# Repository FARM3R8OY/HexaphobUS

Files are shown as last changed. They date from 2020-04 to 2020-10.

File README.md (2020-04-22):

<div id="hexaphobus-logo" align="center">
    <br />
    HexaphobUS Logo
    <h1>HexaphobUS</h1>
    <h3>Hexapod robot | UdeS-GRO</h3>
</div>

[//]: # (------------------------------------------------)

<div id="badges" align="center">
    


 

</div>

[//]: # (------------------------------------------------)

**This is an academic project from robotic engineering undergraduates at Université de Sherbrooke. We are building a 6-axis robot from scratch with motion control, sequencing, and an intuitive user interface.**

<div id="robot" align="center">
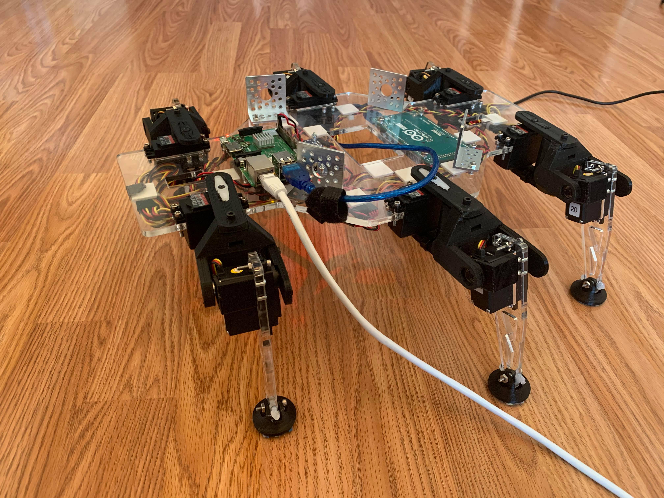
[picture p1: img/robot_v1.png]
Robot
    
</div>

## Table of Contents
- [Setup](#Setup)
    - [Setup for Users](#SetupUsers)
    - [Setup for Repository Contributors](#SetupContrib)
- [Documentation](#Documentation)
- [Robot Operation](#Operation)
- [External Resources](#Resources)
    - [Battery, Power Source, and Charger](#Battery)
    - [Crimping Tool Kit](#Crimp)
    - [Microcontroller Board](#Controller)
    - [On-Board Computer](#Computer)
    - [PWM Servo Driver](#PWM)
    - [Servomotor](#Servo)
    - [Voltage Regulator](#Regulator)
    
[//]: # (------------------------------------------------)

## Setup

#### Setup for Users

- Clone or download the repository;
- Connect the hexapod's microcontroller (Arduino) to your computer;
- Open the file ```hexaphobus_pwm.ino``` in the *./Code/hexaphobus_pwm* folder, and build the code into the microcontroller with your favorite IDE;
- Disconnect the microcontroller and connect the on-board computer (Raspberry Pi) instead (or connect remotely);
- Verify your Python version (3.5 and above);
- Run the file ```hexaphobus_ui.py``` in the *./Code/hexaphobus_ui* folder;
- Initialize the serial communication.

#### Setup for Repository Contributors

To setup the Git, the Key Management System and/or the Integrated Development Environment, head over to the [code setup file](./Code/setup.md). You can also add your own method, so the file can act as a setup archive for various softwares and operating systems.

To add new functions, refine the code, redesign the 3D model, and more, fork your own copy of the repository and [make a pull request after modifications](http://makeapullrequest.com).

## Documentation

All the code documentation can be found [here](https://raw.githack.com/gabrielcabana21/HexaphobUS/code/docs/html/index.html).

## Robot Operation

<div id="hexaphobus-ui" align="center">
    <br />
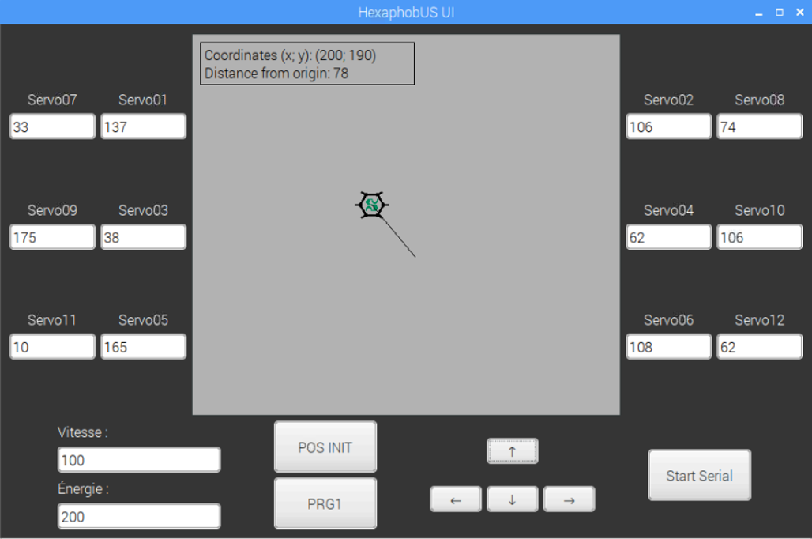
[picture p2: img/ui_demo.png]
HexaphobUS UI
    
</div>

- &#8593;: forward motion;
- &#8595;: backward motion;
- &#8592;: left turn;
- &#8594;: right turn;
- <kbd>POS INIT</kbd>: resets the robot origin;
- <kbd>PRG1</kbd>: pre-programmed motion sequence (currently unused);
- <kbd>Start Serial</kbd>: initializes serial communication with the robot;
- Servo ##: displays the servomotor angle (position of servos on the interface mimicks the robot seen from above);
- Vitesse / Énergie: robot speed and energy consumption (currently unused).

## External Resources

Under this section, you will find external links and descriptions of the project's external resources.

#### Battery, Power Source, and Charger
- Brand Name: Makita
- Model:
    - Battery: BL1041B
    - Power Source: PE00000028
    - Charger: DC10SB
- ASIN:
    - Battery: B017GQJDVM
    - Charger: B01FY4XCB0
- Information / Resources:
    - [Makita Battery Webpage](https://www.makitatools.com/products/details/BL1041B)
    - [Makita Power Source Webpage](https://www.makitatools.com/products/details/PE00000028)
    - [Makita Charger Webpage](https://www.makitatools.com/products/details/DC10SB)

#### Crimping Tool Kit
- Brand Name: Preciva Dupont
- Model: PR-3245 (SN-28B) + JST-XH
- ASIN: B07R1H3Z8X
- Information / Resources: [Amazon Link](https://www.amazon.com/gp/product/B07R1H3Z8X/)

#### Microcontroller Board
- Brand Name: Arduino
- Model: Mega 2560 R3 (A000067)
- ASIN: B0046AMGW0
- Information / Resources: [Arduino Webpage](https://store.arduino.cc/mega-2560-r3)

#### On-Board Computer
- Brand Name: Raspberry Pi
- Model: 3B
- ASIN: B01LPLPBS8
- Information / Resources: [Raspberry Pi Webpage](https://www.raspberrypi.org/products/raspberry-pi-3-model-b/)

#### PWM Servo Driver
- Brand Name: SunFounder
- Model: PCA9685
- ASIN: B014KTSMLA
- Information / Resources: [Sunfounder Wiki](http://wiki.sunfounder.cc/index.php?title=PCA9685_16_Channel_12_Bit_PWM_Servo_Driver)

#### Servomotor
- Brand Name: Hitec RCD
- Model: HS-422
- ASIN: B0006O3WWI
- Information / Resources: [Hitec Webpage](https://hitecrcd.com/products/servos/sport-servos/analog-sport-servos/hs-422/product)

#### Voltage Regulator
- Brand Name: DROK
- Model: 090483
- ASIN: B00C4QVTNU
- Information / Resources: [DROK Webpage](https://www.droking.com/Adjustable-High-Power-Adapter-Buck-Voltage-Regulator-DC8-40V-to-1.25-36V-8A-100W-Converter-Laptop-Charger)

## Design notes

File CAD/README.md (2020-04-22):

## Parts and Assemblies
- Assemblies:
  - [V1](./V1)
  - [V2](./V2)
  - [V3](./V3)
- Internal resources (homemade components):
  - [V1](./V1/Internal)
  - [V2](./V2/Internal)
  - [V3](./V3/Internal)
- [External resources](./External)
- [Files for laser cutting](./Cutting)

The hexapod was designed with only a coxa motor and a tibia motor, omitting the femur motor to minimise the power requirement. Most motion types should be feasible, albeit a little more limited. Legs on each side of the body are designed symmetrically to align the feet and facilitate the body design (mirrored sketches). They each contain a foot, two motors, two bearings and their mounts, a joint and its two attachments, and some screws and bolts. The hexapod assembly contains six legs, three of which are mirrored, an on-board computer, a microcontroller board, a voltage regulator, a PWM servo driver, a battery, and some fasteners.

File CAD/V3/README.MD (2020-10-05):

<div id="hexaphobus-robot-v3-hex" align="center">
    <br />
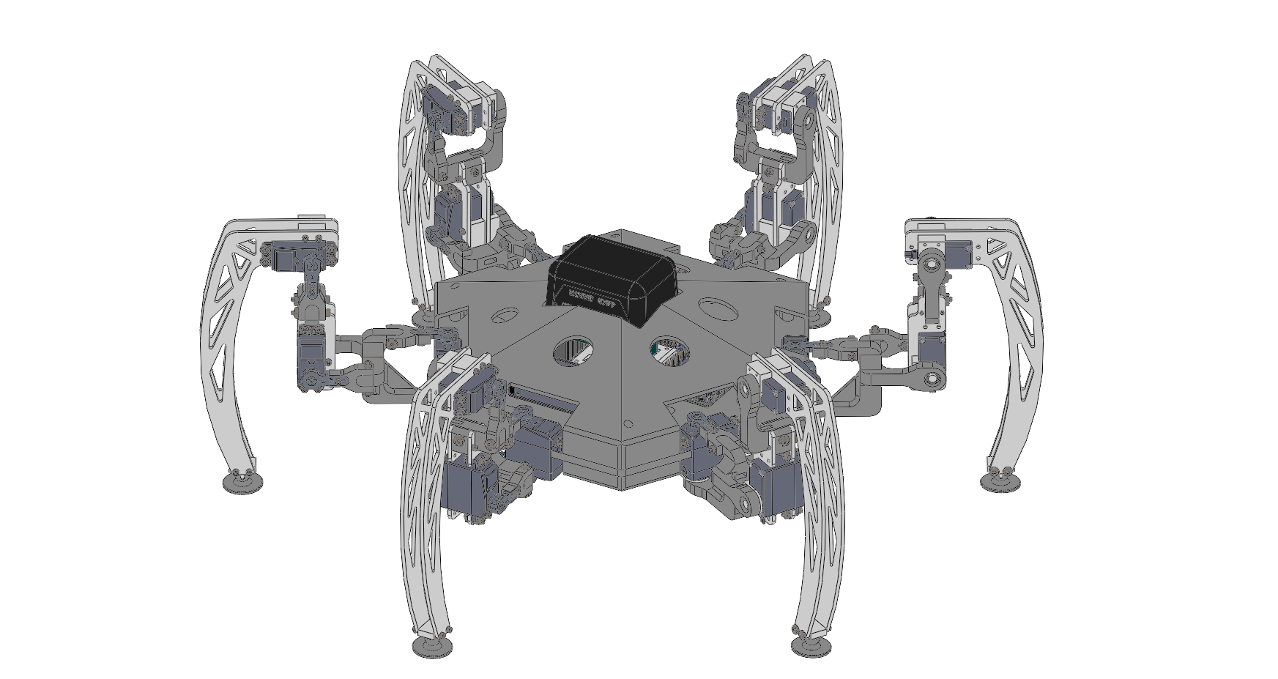
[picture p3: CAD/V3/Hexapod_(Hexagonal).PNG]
HexaphobUS Robot (V3, Hexagonal)
    
</div>

<div id="hexaphobus-robot-v3-18m" align="center">
    <br />
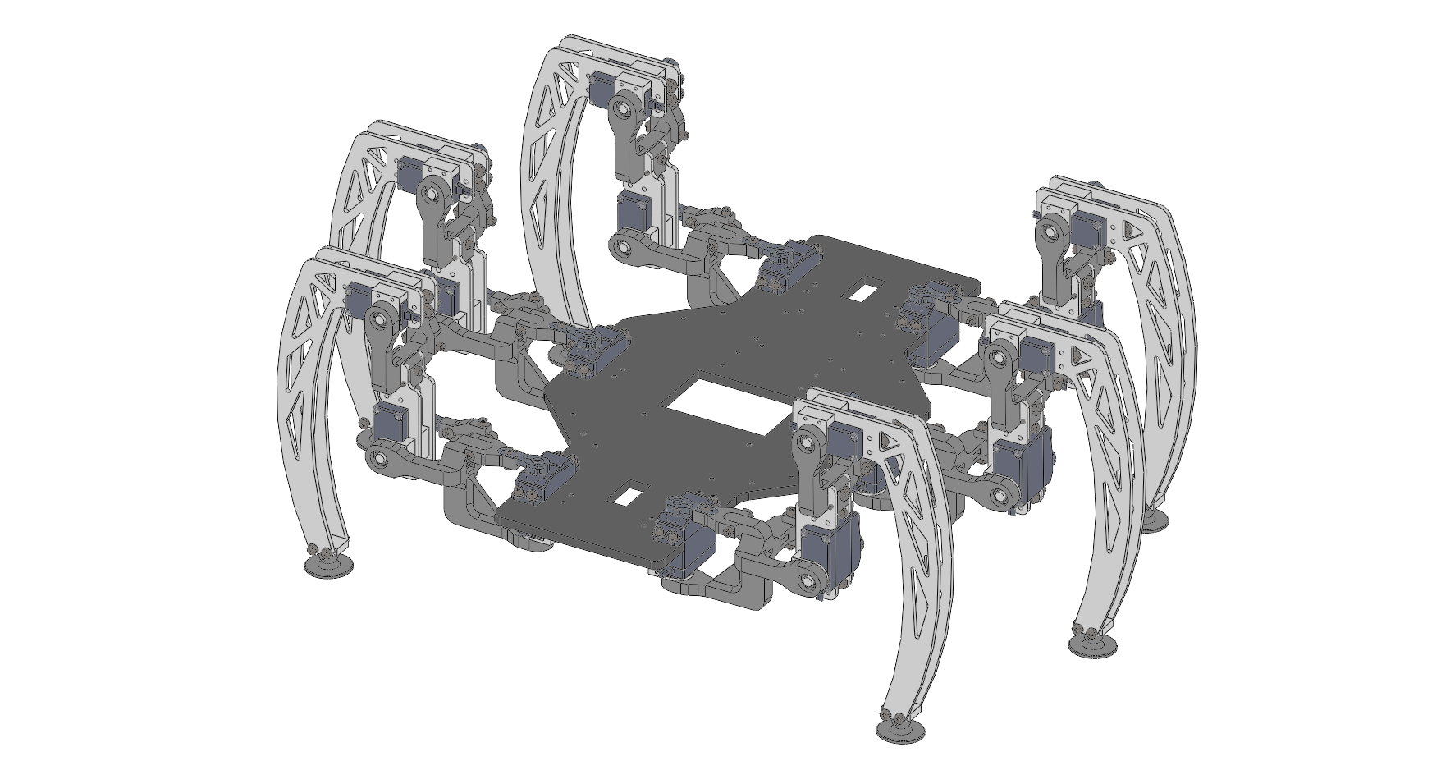
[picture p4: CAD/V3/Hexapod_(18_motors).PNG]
HexaphobUS Robot (V3, 18 Motors)
    
</div>

<div id="hexaphobus-robot-v3-12m" align="center">
    <br />
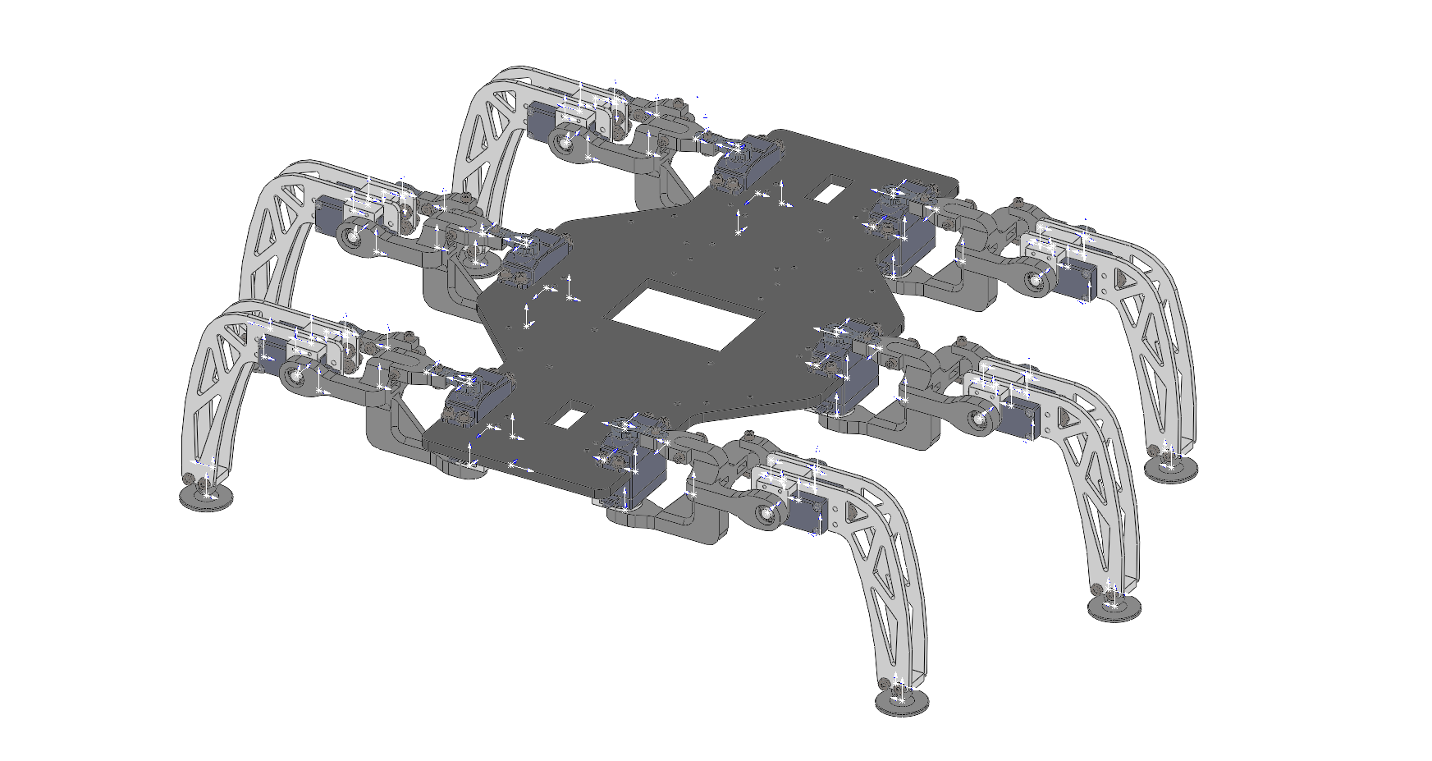
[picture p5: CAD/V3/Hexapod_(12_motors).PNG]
HexaphobUS Robot (V3, 12 Motors)
    
</div>

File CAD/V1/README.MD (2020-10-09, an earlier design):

<div id="hexaphobus-robot-v1-curved" align="center">
    <br />
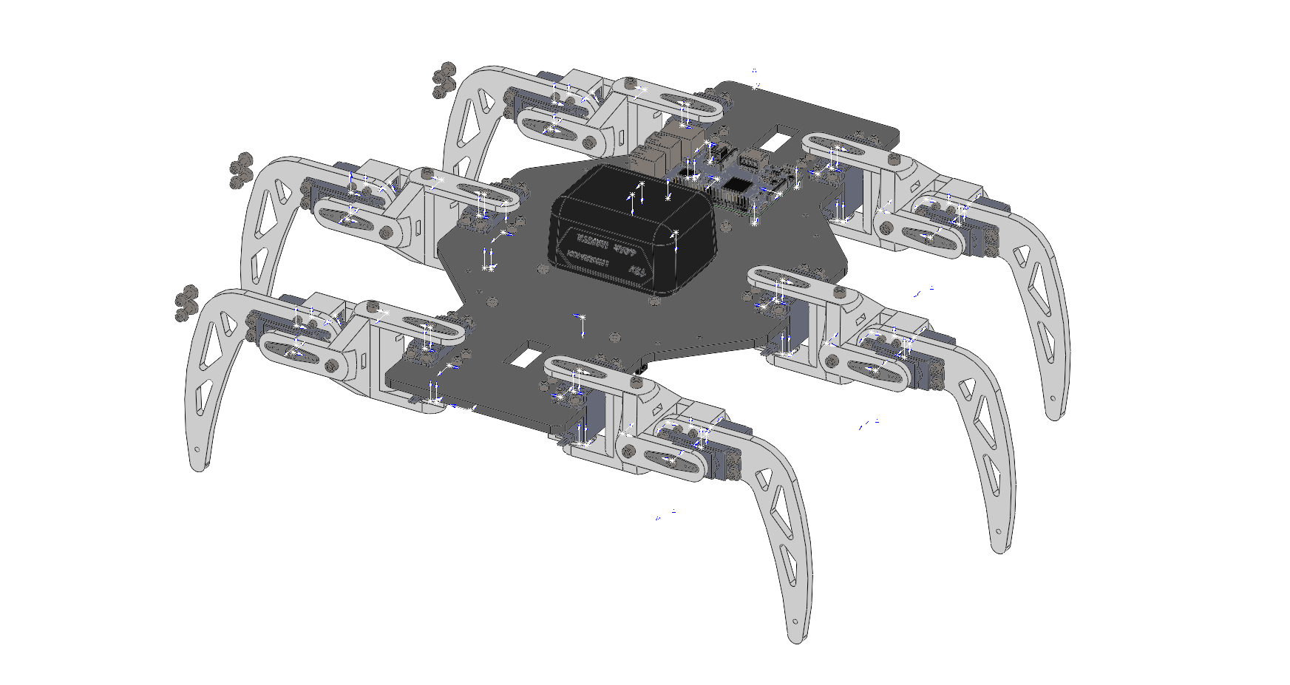
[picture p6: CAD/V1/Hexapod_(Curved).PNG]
HexaphobUS Robot (V1, Curved Legs)
    
</div>

<div id="hexaphobus-robot-v1-straight" align="center">
    <br />
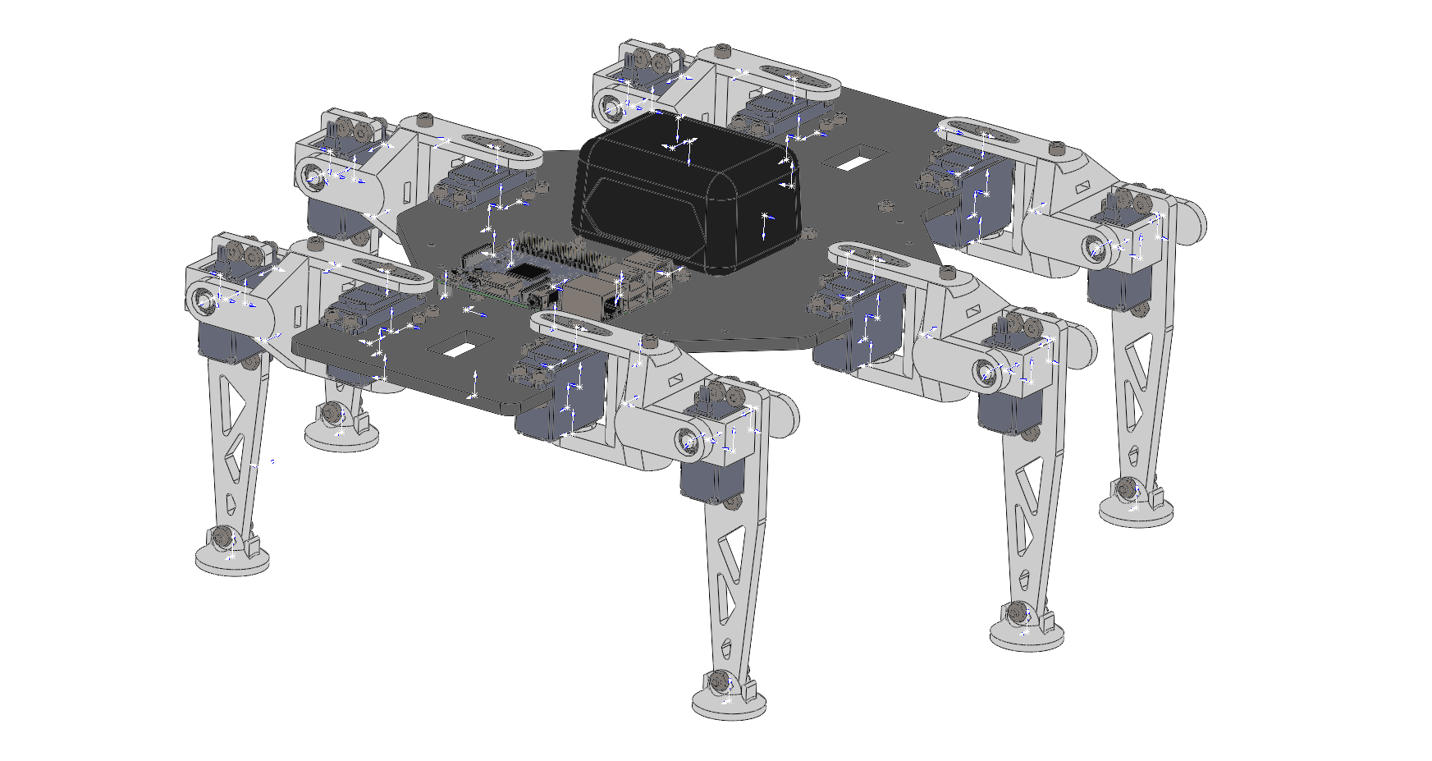
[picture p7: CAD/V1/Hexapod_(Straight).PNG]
HexaphobUS Robot (V1, Straight Legs)
    
</div>

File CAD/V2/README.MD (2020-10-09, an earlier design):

<div id="hexaphobus-robot-v2" align="center">
    <br />
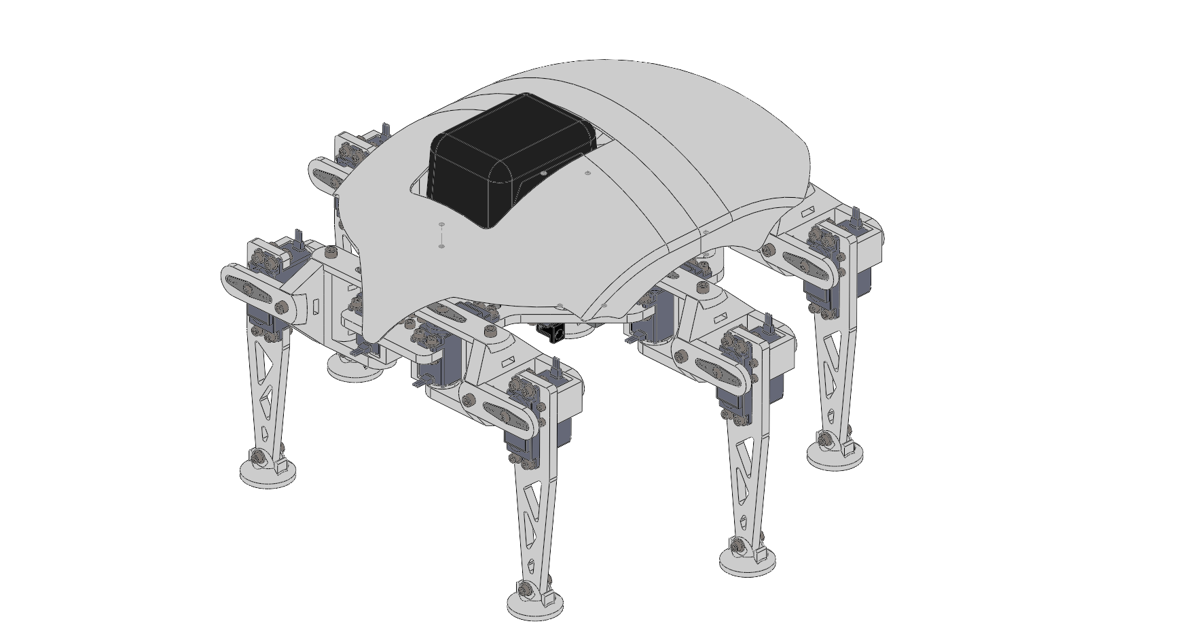
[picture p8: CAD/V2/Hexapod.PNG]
HexaphobUS Robot (V2)
    
</div>

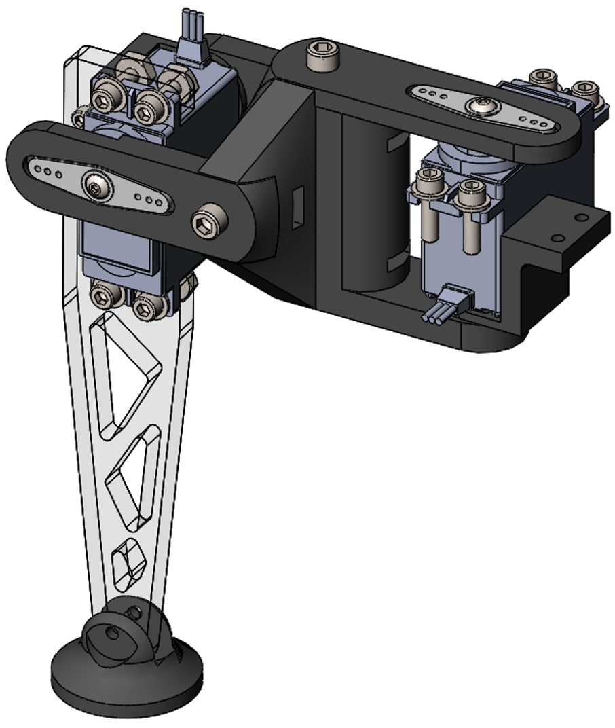
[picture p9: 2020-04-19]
img/leg_design_v2.png

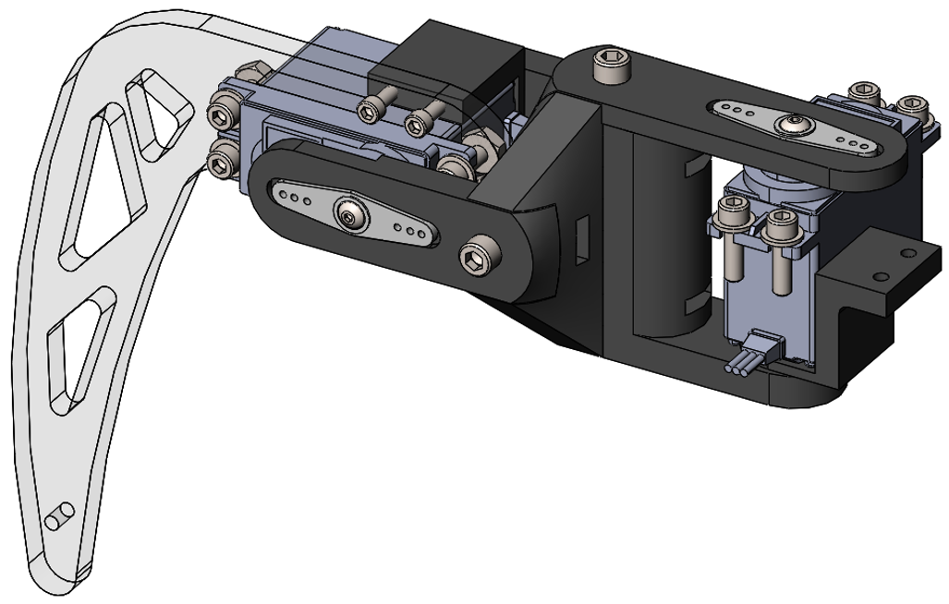
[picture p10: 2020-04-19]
img/leg_design_v1_(1).png

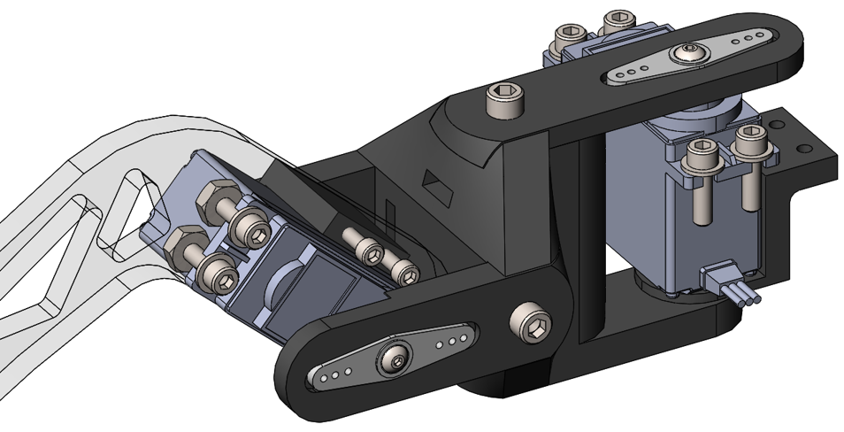
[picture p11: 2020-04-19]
img/leg_design_v1_(2).png

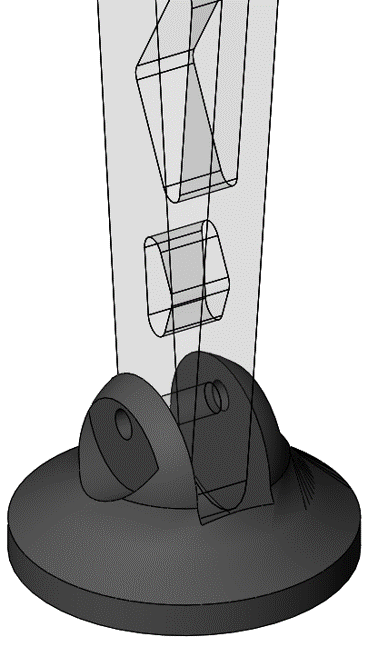
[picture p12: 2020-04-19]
img/slippers.png

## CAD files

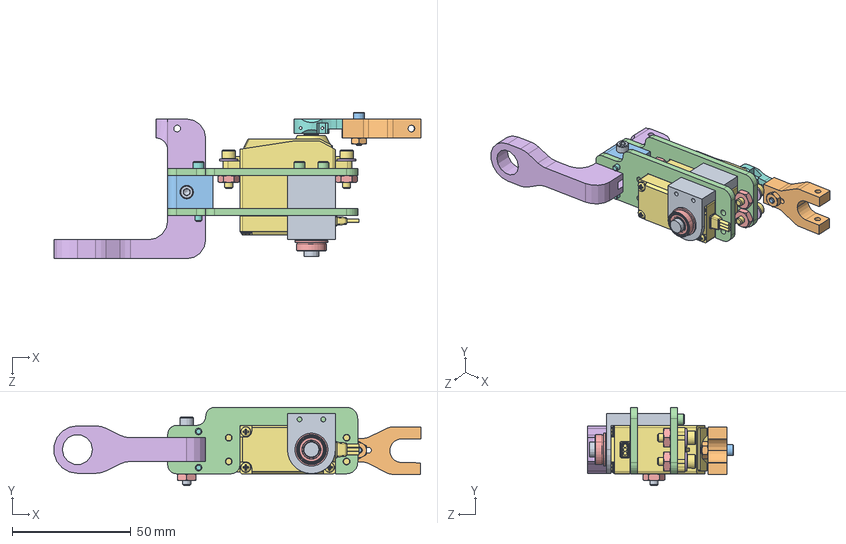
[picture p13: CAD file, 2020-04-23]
CAD/V3/Tibia_(Mirror).SLDASM
154.5 x 33.0 x 61.6 mm
Link
Horn_attachment
Joint_attachment_(Tibia)
Tibia x 2
Bearing
Joint_(Tibia_to_foot)
DS3225MG
Horn
Bearing_mount_(Foot)
MSHXNUT 0.112-40-D-N
HX-SHCS 0.112-40x0.4375x0.4375-N
HX-SHCS 0.112-40x1x0.75-N x 2
MSHXNUT 0.138-32-D-N x 5
Narrow FW 0.138 x 4
HX-SHCS 0.138-32x0.5x0.5-N x 4
HX-SHCS 0.112-40x0.875x0.875-N x 2
HX-SHCS 0.138-32x1x1-N

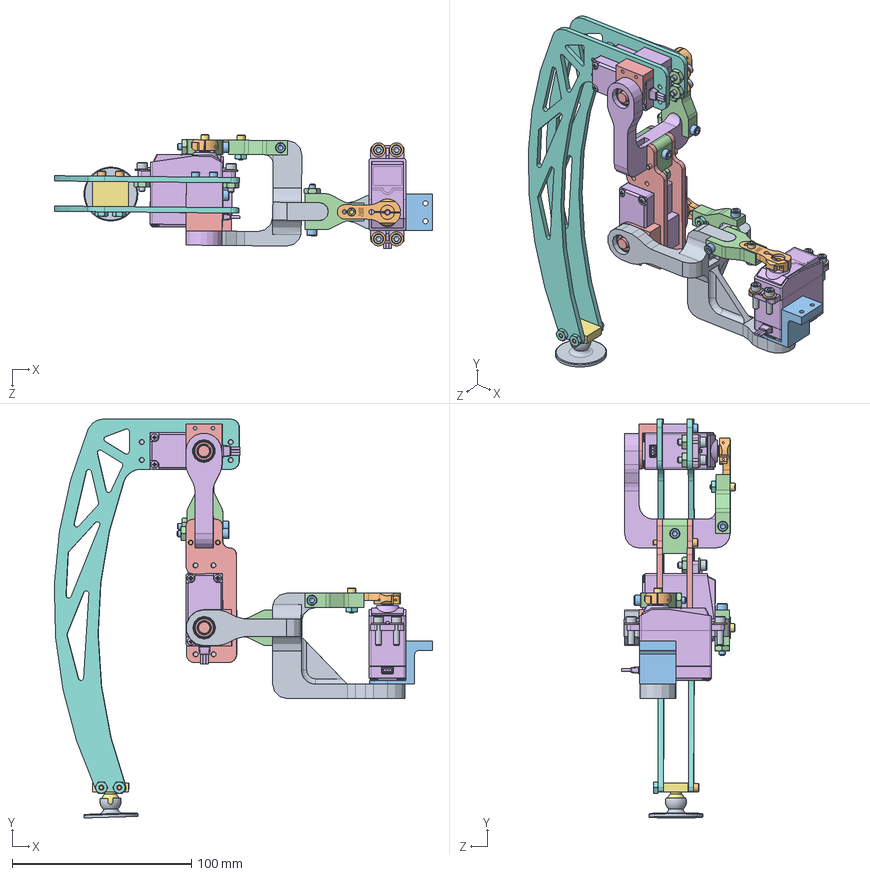
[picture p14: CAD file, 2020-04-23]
CAD/V3/Foot+Tibia+Femur_(Mirror).SLDASM
210.9 x 222.5 x 63.4 mm
Joint_(Femur_to_tibia)_(Mirror)
Horn x 3
Bearing_mount_(Femur)
Horn_attachment x 3
Bearing x 3
DS3225MG x 3
HX-SHCS 0.112-40x0.4375x0.4375-N x 3
MSHXNUT 0.112-40-D-N x 5
HX-SHCS 0.138-32x0.5x0.5-N x 12
Narrow FW 0.138 x 12
HX-SHCS 0.138-32x1x1-N x 4
MSHXNUT 0.138-32-D-N x 12
Bearing_mount_(Foot) x 2
Link x 2
Joint_(Foot_to_slipper)
Foot_(Long) x 2
Slipper
HX-SHCS 0.112-40x0.875x0.875-N x 4
HX-SHCS 0.112-40x1x0.75-N x 4
Joint_attachment_(Tibia)
Tibia x 2
Joint_(Tibia_to_foot)

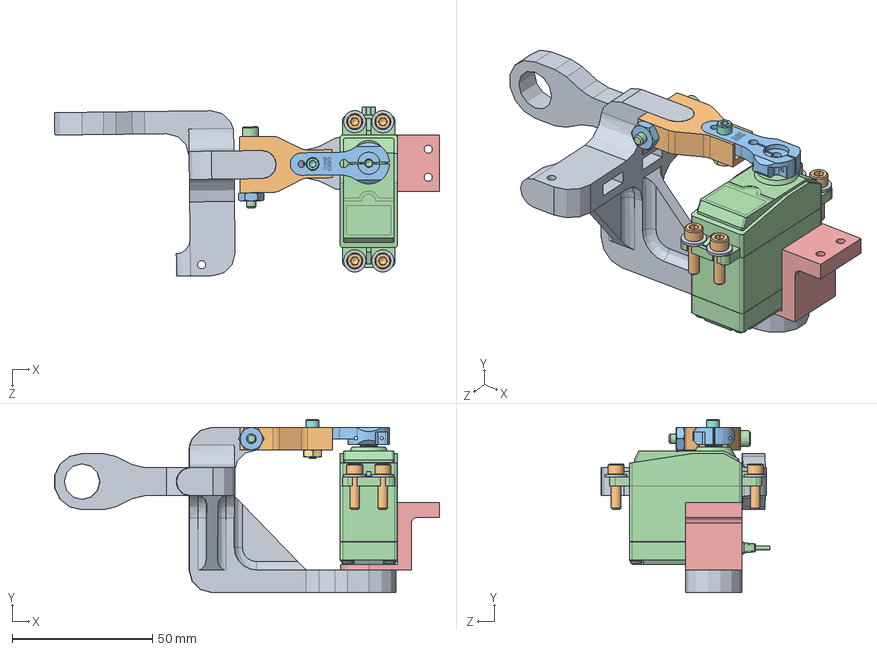
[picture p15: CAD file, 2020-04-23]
CAD/V3/Femur.SLDASM
137.2 x 61.6 x 60.3 mm
Joint_(Femur_to_tibia)
Horn_attachment
Horn
DS3225MG
Bearing_mount_(Femur)
Bearing
MSHXNUT 0.112-40-D-N
HX-SHCS 0.112-40x0.4375x0.4375-N
Narrow FW 0.138 x 4
HX-SHCS 0.138-32x0.5x0.5-N x 4
MSHXNUT 0.138-32-D-N
HX-SHCS 0.138-32x1x1-N

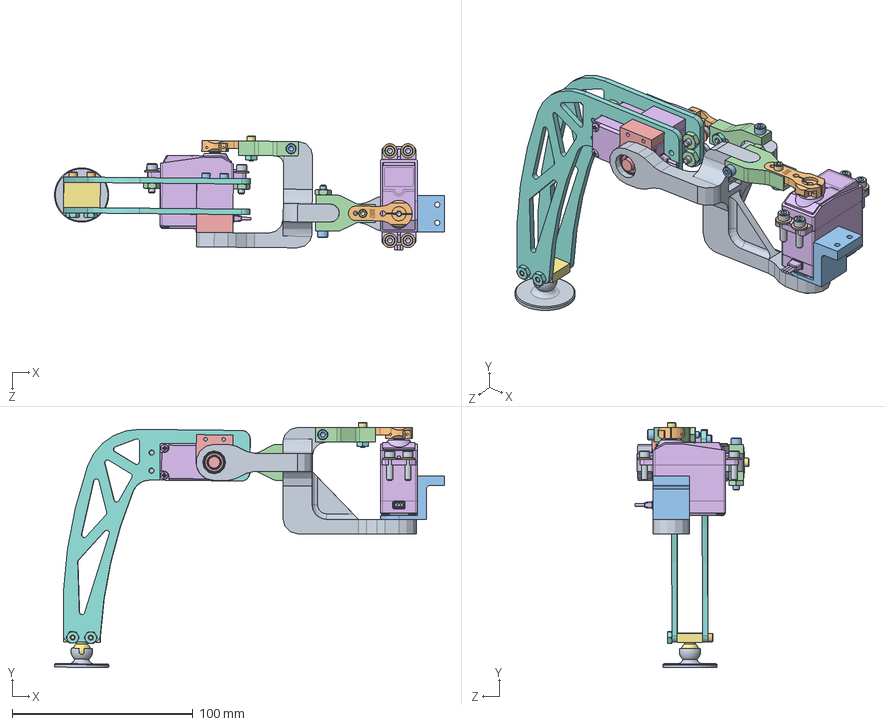
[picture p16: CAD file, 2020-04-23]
CAD/V3/Foot+Femur_(Mirror).SLDASM
215.7 x 135.7 x 63.2 mm
Joint_(Femur_to_tibia)_(Mirror)
Horn x 2
Bearing_mount_(Femur)
Horn_attachment x 2
Bearing x 2
DS3225MG x 2
HX-SHCS 0.112-40x0.4375x0.4375-N x 2
MSHXNUT 0.112-40-D-N x 4
HX-SHCS 0.138-32x0.5x0.5-N x 8
Narrow FW 0.138 x 8
HX-SHCS 0.138-32x1x1-N x 2
MSHXNUT 0.138-32-D-N x 6
Bearing_mount_(Foot)
Link
Joint_(Foot_to_slipper)
Foot_(Short) x 2
Slipper
HX-SHCS 0.112-40x0.875x0.875-N x 2
HX-SHCS 0.112-40x1x0.75-N x 2

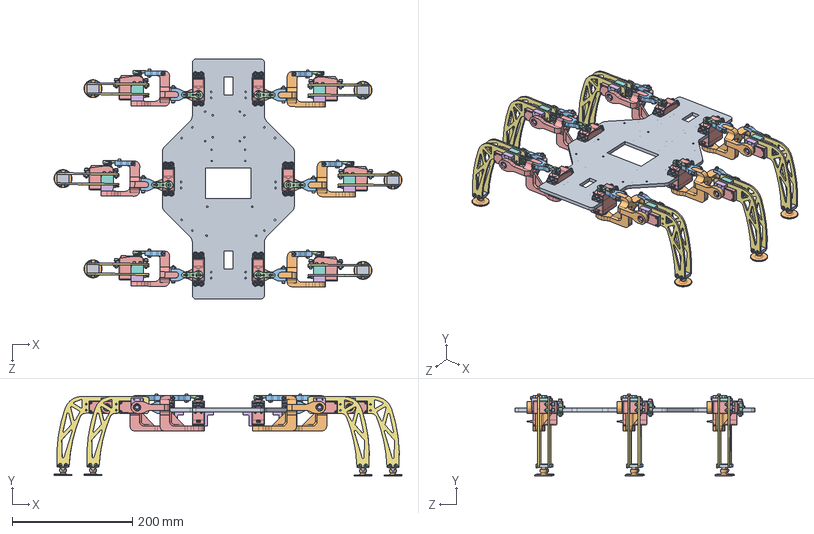
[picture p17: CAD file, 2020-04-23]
CAD/V3/Hexapod_(12_motors).SLDASM
579.5 x 136.5 x 400.0 mm
Joint_(Femur_to_tibia) x 3
Horn_attachment x 12
Horn x 12
DS3225MG x 12
Bearing_mount_(Femur) x 6
Bearing x 12
MSHXNUT 0.112-40-D-N x 24
HX-SHCS 0.112-40x0.4375x0.4375-N x 12
Narrow FW 0.138 x 48
HX-SHCS 0.138-32x0.5x0.5-N x 48
MSHXNUT 0.138-32-D-N x 36
HX-SHCS 0.138-32x1x1-N x 12
Bearing_mount_(Foot) x 6
Foot_(Short) x 12
Link x 6
Joint_(Foot_to_slipper) x 6
Slipper x 6
HX-SHCS 0.112-40x0.875x0.875-N x 12
HX-SHCS 0.112-40x1x0.75-N x 12
Joint_(Femur_to_tibia)_(Mirror) x 3

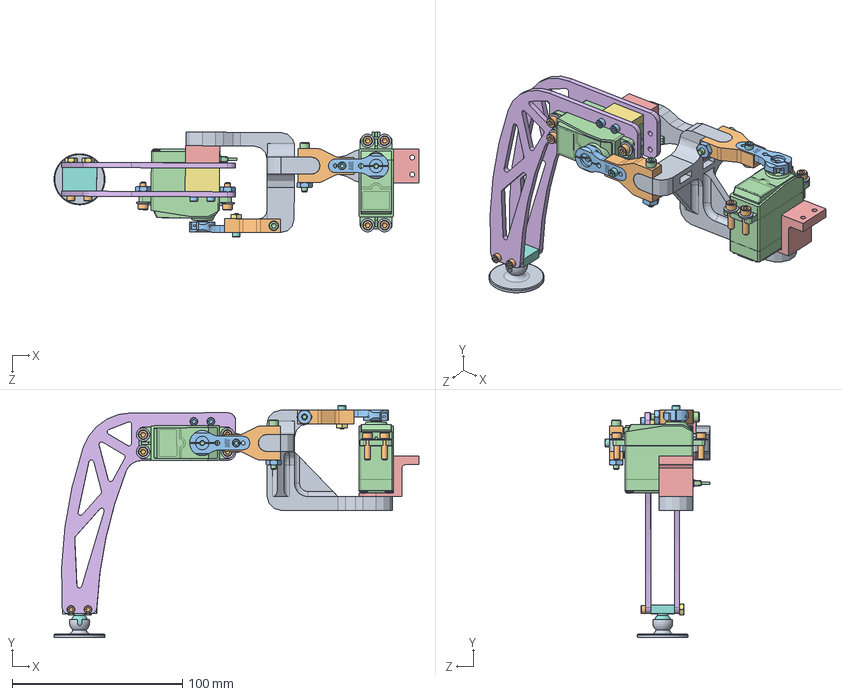
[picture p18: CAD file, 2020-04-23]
CAD/V3/Foot+Femur.SLDASM
214.5 x 136.5 x 62.0 mm
Joint_(Femur_to_tibia)
Horn_attachment x 2
Horn x 2
DS3225MG x 2
Bearing_mount_(Femur)
Bearing x 2
MSHXNUT 0.112-40-D-N x 4
HX-SHCS 0.112-40x0.4375x0.4375-N x 2
Narrow FW 0.138 x 8
HX-SHCS 0.138-32x0.5x0.5-N x 8
MSHXNUT 0.138-32-D-N x 6
HX-SHCS 0.138-32x1x1-N x 2
Bearing_mount_(Foot)
Foot_(Short) x 2
Link
Joint_(Foot_to_slipper)
Slipper
HX-SHCS 0.112-40x0.875x0.875-N x 2
HX-SHCS 0.112-40x1x0.75-N x 2

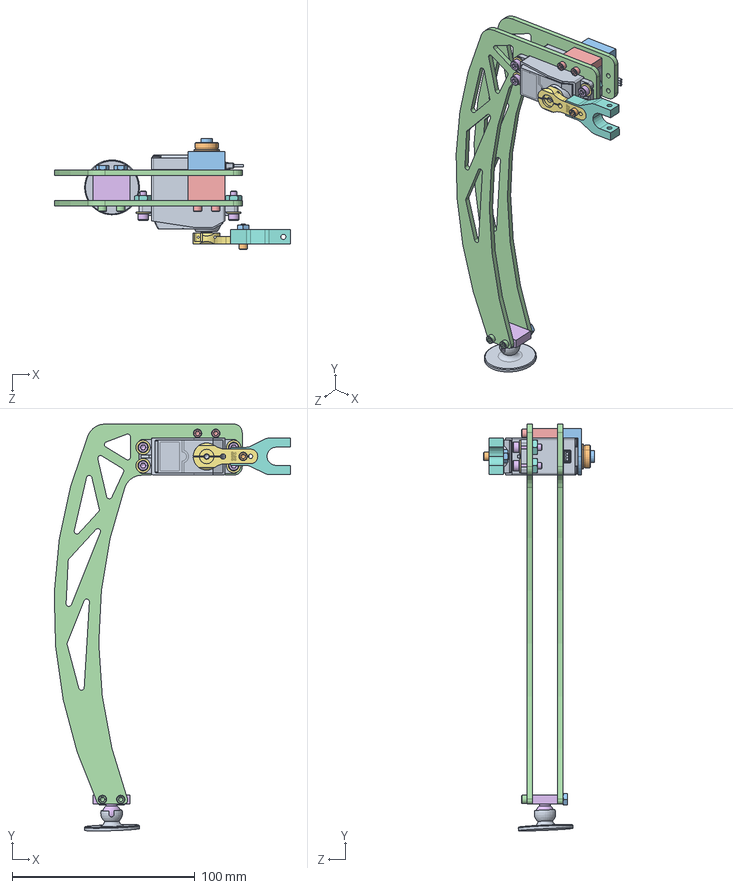
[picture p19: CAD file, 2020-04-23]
CAD/V3/Foot_(Long).SLDASM
129.5 x 222.8 x 60.6 mm
DS3225MG
Bearing
Bearing_mount_(Foot)
Foot_(Long) x 2
Link
Joint_(Foot_to_slipper)
Horn
Horn_attachment
Slipper
HX-SHCS 0.112-40x0.4375x0.4375-N
MSHXNUT 0.112-40-D-N x 3
HX-SHCS 0.112-40x0.875x0.875-N x 2
HX-SHCS 0.112-40x1x0.75-N x 2
HX-SHCS 0.138-32x0.5x0.5-N x 4
Narrow FW 0.138 x 4
MSHXNUT 0.138-32-D-N x 4

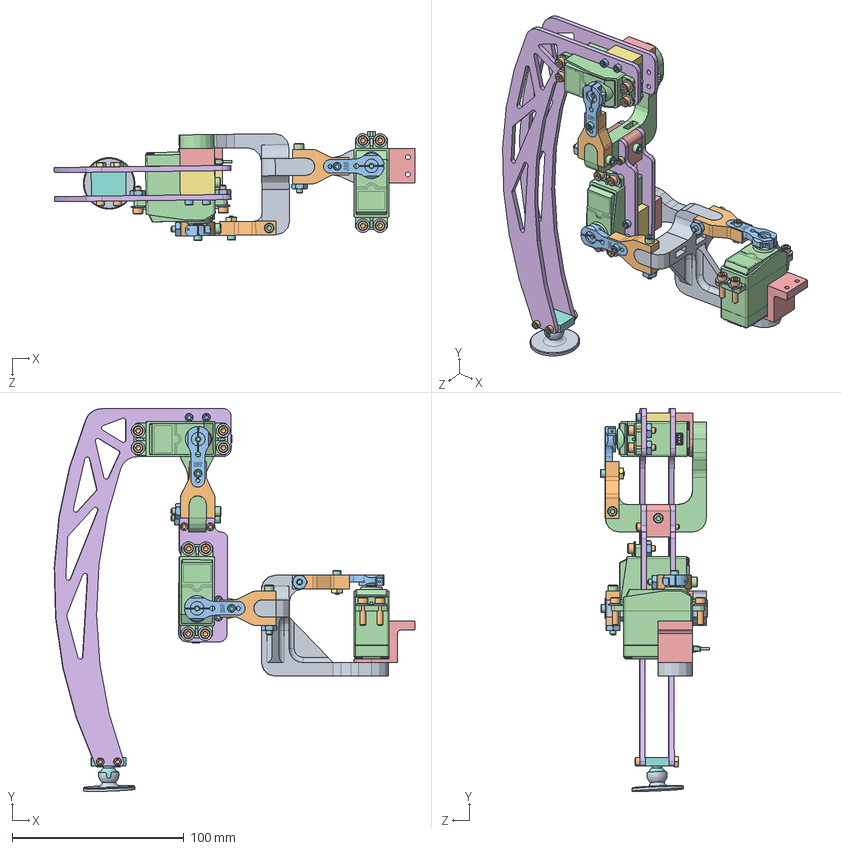
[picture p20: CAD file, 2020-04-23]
CAD/V3/Foot+Tibia+Femur.SLDASM
209.9 x 222.9 x 63.6 mm
Joint_(Femur_to_tibia)
Horn_attachment x 3
Horn x 3
DS3225MG x 3
Bearing_mount_(Femur)
Bearing x 3
MSHXNUT 0.112-40-D-N x 5
HX-SHCS 0.112-40x0.4375x0.4375-N x 3
Narrow FW 0.138 x 12
HX-SHCS 0.138-32x0.5x0.5-N x 12
MSHXNUT 0.138-32-D-N x 12
HX-SHCS 0.138-32x1x1-N x 4
Bearing_mount_(Foot) x 2
Foot_(Long) x 2
Link x 2
Joint_(Foot_to_slipper)
Slipper
HX-SHCS 0.112-40x0.875x0.875-N x 4
HX-SHCS 0.112-40x1x0.75-N x 4
Joint_(Tibia_to_foot)
Joint_attachment_(Tibia)
Tibia x 2

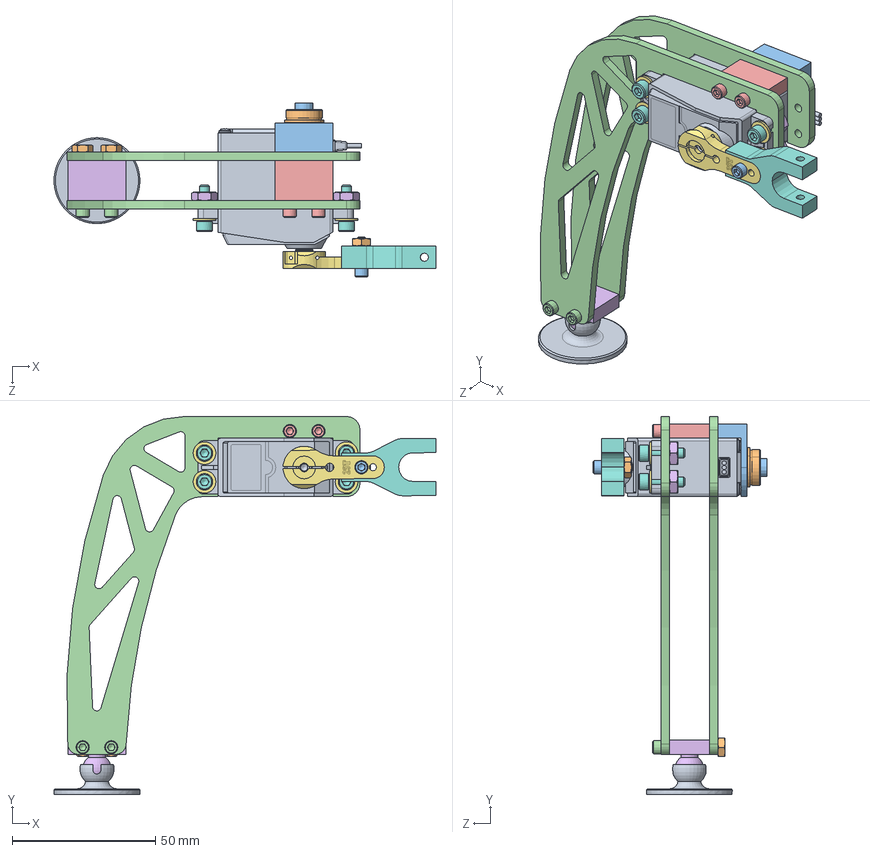
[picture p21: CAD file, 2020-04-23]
CAD/V3/Foot_(Short).SLDASM
133.4 x 132.0 x 60.6 mm
DS3225MG
Bearing
Bearing_mount_(Foot)
Foot_(Short) x 2
Link
Joint_(Foot_to_slipper)
Horn
Horn_attachment
Slipper
MSHXNUT 0.112-40-D-N x 3
HX-SHCS 0.112-40x0.4375x0.4375-N
HX-SHCS 0.112-40x0.875x0.875-N x 2
HX-SHCS 0.112-40x1x0.75-N x 2
MSHXNUT 0.138-32-D-N x 4
Narrow FW 0.138 x 4
HX-SHCS 0.138-32x0.5x0.5-N x 4

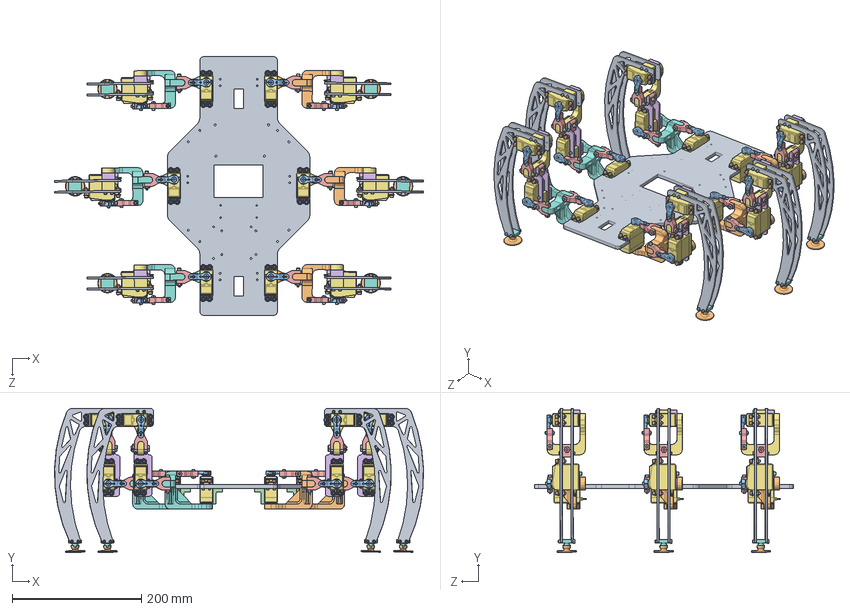
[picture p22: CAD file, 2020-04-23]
CAD/V3/Hexapod_(18_motors).SLDASM
570.2 x 223.0 x 400.0 mm
Joint_(Femur_to_tibia)_(Mirror) x 3
Horn x 18
Bearing_mount_(Femur) x 6
Horn_attachment x 18
Bearing x 18
DS3225MG x 18
HX-SHCS 0.112-40x0.4375x0.4375-N x 18
MSHXNUT 0.112-40-D-N x 30
HX-SHCS 0.138-32x0.5x0.5-N x 72
Narrow FW 0.138 x 72
HX-SHCS 0.138-32x1x1-N x 24
MSHXNUT 0.138-32-D-N x 72
Bearing_mount_(Foot) x 12
Link x 12
Joint_(Foot_to_slipper) x 6
Foot_(Long) x 12
Slipper x 6
HX-SHCS 0.112-40x0.875x0.875-N x 24
HX-SHCS 0.112-40x1x0.75-N x 24
Joint_attachment_(Tibia) x 6
Tibia x 12
Joint_(Tibia_to_foot) x 6
Joint_(Femur_to_tibia) x 3

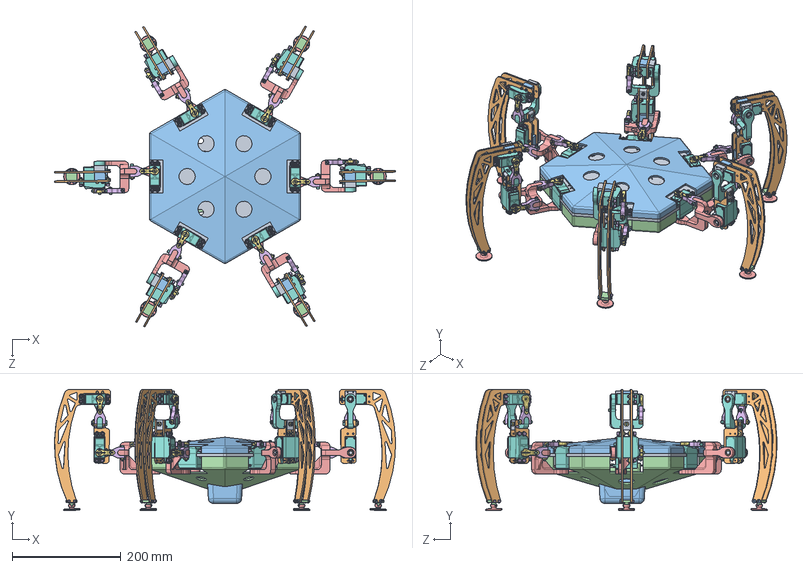
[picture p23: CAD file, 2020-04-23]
CAD/V3/Hexapod_(Hexagonal)_(Flipped).SLDASM
627.9 x 222.9 x 554.2 mm
Body_(Hexagonal)
Battery_holder
MAKITA 4.0AH
MAKITA 4.0AH MOBILE
Joint_(Femur_to_tibia) x 6
Horn_attachment x 18
Horn x 18
DS3225MG x 18
Bearing_mount_(Femur) x 6
Bearing x 18
MSHXNUT 0.112-40-D-N x 30
HX-SHCS 0.112-40x0.4375x0.4375-N x 18
Narrow FW 0.138 x 72
HX-SHCS 0.138-32x0.5x0.5-N x 72
MSHXNUT 0.138-32-D-N x 72
HX-SHCS 0.138-32x1x1-N x 24
Bearing_mount_(Foot) x 12
Foot_(Long) x 12
Link x 12
Joint_(Foot_to_slipper) x 6
Slipper x 6
HX-SHCS 0.112-40x0.875x0.875-N x 24
HX-SHCS 0.112-40x1x0.75-N x 24
Joint_(Tibia_to_foot) x 6
Joint_attachment_(Tibia) x 6
Tibia x 12
Shell_(Bottom)
Shell_(Top)

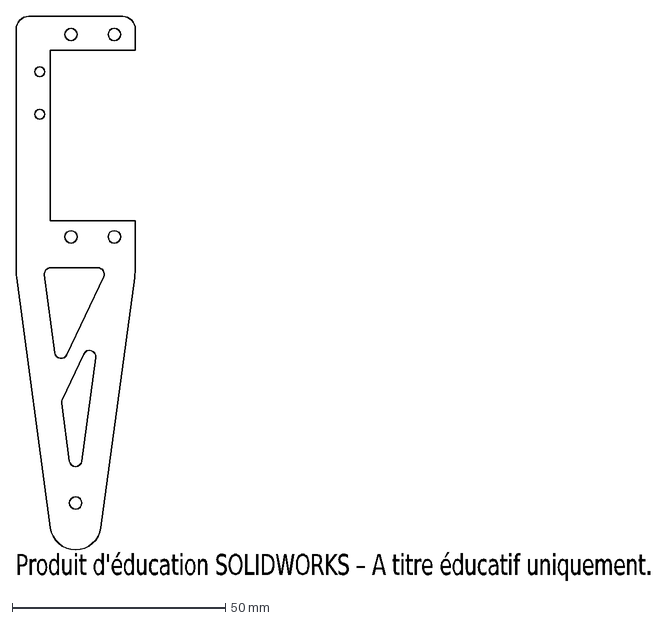
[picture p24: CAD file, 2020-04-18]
CAD/Cutting/Foot_(Straight).DXF
Produit d'éducation SOLIDWORKS – A titre éducatif uniquement.

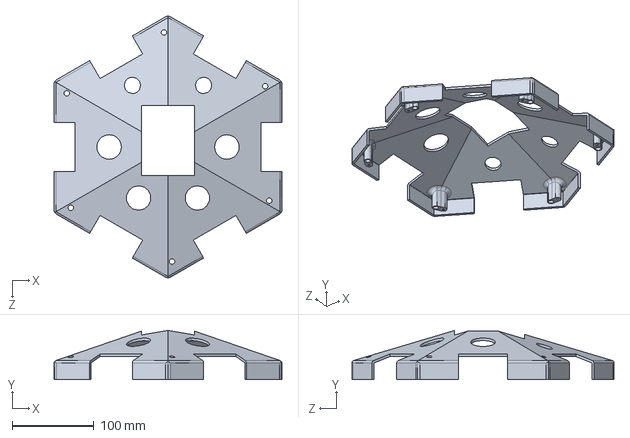
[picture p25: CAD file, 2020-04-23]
CAD/V3/Internal/Shell_(Top).SLDPRT
278.7 x 60.1 x 320.0 mm

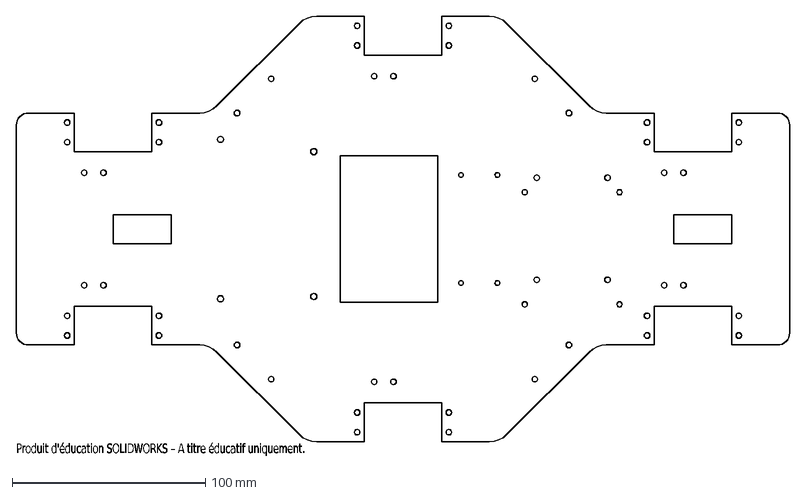
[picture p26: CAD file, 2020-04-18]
CAD/Cutting/Body.DXF
Produit d'éducation SOLIDWORKS – A titre éducatif uniquement.

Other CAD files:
CAD/V3/Foot_(Long)_(Mirror).SLDASM
CAD/V3/Femur_(Mirror).SLDASM
CAD/V3/Tibia.SLDASM
CAD/V3/Foot_(Short)_(Mirror).SLDASM
CAD/V1/Internal/Bearing_mount_leg.SLDPRT
CAD/V1/Internal/Body.SLDPRT
CAD/V1/Internal/Foot_(Curved).SLDPRT
CAD/V1/Internal/Foot_(Straight).SLDPRT
CAD/V1/Internal/Joint.SLDPRT
CAD/V1/Internal/Joint_(Mirror).SLDPRT
CAD/V1/Internal/Joint_attachment_foot.SLDPRT
CAD/V1/Internal/Joint_attachment_leg.SLDPRT
CAD/V1/Internal/Slipper.SLDPRT
CAD/V1/Internal/bearing_mount_foot.SLDPRT
CAD/V1/Leg_(Curved_Foot).SLDASM
CAD/V1/Leg_(Curved_Foot)_(Mirror).SLDASM
CAD/V1/Leg_(Straight_Foot).SLDASM
CAD/V1/Leg_(Straight_Foot)_(Mirror).SLDASM
CAD/V2/Internal/Battery_holder.SLDPRT
CAD/V2/Internal/Body_(Small).SLDPRT
CAD/V2/Internal/Shell_(Back).SLDPRT
CAD/V2/Internal/Shell_(Front).SLDPRT
CAD/V3/Internal/Battery_holder.SLDPRT
CAD/V3/Internal/Bearing_mount_(Femur).SLDPRT
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

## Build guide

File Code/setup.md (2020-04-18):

## Setup
- [Installations](#Install)
	- [Install KMS](#insKMS)
	- [Install Git](#insGit)
	- [Install IDE](#insIDE)
	- [Upgrade Python on Debian (Raspberry Pi)](#PyUpgrade)
- [Key Management](#KeyManage)
	- [Generate keys](#kmGen)
	- [Export keys](#kmExp)
- [Git Configuration](#GitConfig)
	- [Stage, commit and push using Git](#DirectGit)
- [IDE Configuration](#IDEConfig)
	- [Git on VSCode / VSCodium](#IDEGitConfig)
	- [Arduino on VSCode / VSCodium](#IDEArduinoConfig)

[//]: # (------------------------------------------------)

This setup procedure is provided for people who wish to know the details about key management for signed commits, and integration of Git and Arduino in an IDE of their choice. Personally, we chose VSCodium for Windows 10 and Debian 9 (Raspberry Pi 3+) as our IDE, with the Arduino IDE as a dependency, and GnuPG as our key management system.

Notes:
- Git integration might be easier with GitHub Desktop or GitKraken. To be explored.
- Key management can also work with an SSH protocol. To be explored.
- If you wish to add your own procedure to this file, contact one of the contributors.

[//]: # (------------------------------------------------)

## Installations

#### Install Key Management System (KMS)

- Linux: [GnuPG](https://www.gnupg.org/download/)
- Mac: [GnuPG for OS X](https://sourceforge.net/p/gpgosx/docu/Download/) and [GPG tools](https://gpgtools.org/)
- Windows: [Gpg4win](https://gpg4win.org/download.html)

#### Install Git

- [Linux](https://git-scm.com/download/linux)
- [Mac](https://git-scm.com/download/mac)
- [Windows](https://git-scm.com/download/win)

#### Install Integrated Development Environment (IDE)

- [Arduino](https://www.arduino.cc/en/main/software)
- [VSCode](https://code.visualstudio.com/)
- [VSCodium](https://github.com/VSCodium/vscodium/releases)

#### Upgrade Python on Debian (Raspberry Pi)

If you wish to run Python on the latest and greatest on your Raspberry Pi, you must install from the source code. The sequence of command lines is as follows:
- Install prerequisites:
	```bash
	sudo apt-get update
	sudo apt-get install -y build-essential tk-dev libncurses5-dev libncursesw5-dev |
	libreadline6-dev libdb5.3-dev libgdbm-dev libsqlite3-dev libssl-dev libbz2-dev |
	libexpat1-dev liblzma-dev zlib1g-dev libffi-dev openssl tar wget vim
	```
- Download Python:
	```bash
	cd /opt
	wget https://www.python.org/ftp/python/3.8.0/Python-3.8.2.tgz
	```
- Extract: 
	```bash
	sudo tar zxf Python-3.8.2.tgz
	cd Python-3.8.2
	sudo ./configure --enable-optimizations
	sudo make -j 4 # Number of cores on Pi (can be found with command 'nproc')
	sudo make altinstall
	```
- Make it your default version:
	```bash
	python3.8 -V
	echo "alias python=/usr/local/bin/python3.8" >> ~/.bashrc
	source ~/.bashrc
	python -V
	```
- Install modules:
	```bash
	sudo apt-get install python3-pyqt5
	```

Don't forget to delete the archive and the extracted folder after successful installation.

[//]: # (------------------------------------------------)

## Key Management

#### Generate keys

Open Git Bash or Command Prompt, and generate a set of public and private keys.
```bash
gpg --full-generate-key

# For GnuPG version 2.1.16 and below:
gpg --default-new-key-algo rsa4096 --gen-key
```

Following [Github](https://help.github.com/en/github/authenticating-to-github/generating-a-new-gpg-key)'s recommendations:
- Select the default protocol (RSA and RSA);
- Select a 4096 bits key;
- Select an expiration date (none for minimum maintenance);
- Confirm;
- Enter your name (real name, user name, etc.);
- Enter your verified GitHub email adress (**important**);
- Enter a comment (optional);
- Enter a passphrase (this will allow you to access restricted GPG operations and sign your commits).

#### Export keys

Still in Git Bash or Command Prompt, display your newly-created keys.
```bash
gpg --list-secret-keys --keyid-format LONG
```

The resulting text will look something like this:
```bash
	sec   rsa4096/<sec-key-ID> <creation-date> [SC]
	      <long-sec-key-ID>
	uid                 [ultimate] <username> <email@example.com>
	ssb   rsa4096/<ssb-key-ID> <creation-date> [E]
```

Select the public key ID (in the example above, ```<sec-key-ID>```) and run the GPG export command.
```bash
gpg --armor --export <sec-key-ID>
```

The entire public key should now be displayed:
```bash
-----BEGIN PGP PUBLIC KEY BLOCK-----
*Huge chunk of characters*
-----END PGP PUBLIC KEY BLOCK-----
```

Copy the entire output, and setup a new GPG key on [GitHub](https://github.com/settings/keys).

Now we only need to register the public key to the GnuPG server, in order for the signed commits to work properly.
- Run ```gpg --gen-revoke <sec-key-ID>```;
- Confirm the revocation certificate;
- Run ```gpg --send-keys <sec-key-ID>``` (**this only sends the public key**).

The key management procedure is now complete. You can close the window.

[//]: # (------------------------------------------------)

## Git Configuration

The Git configuration can be managed at a local or a global level, depending on your needs. For our purposes, we will use a global config.

Open the Windows Command Prompt and run the following commands. If any issue is encountered later on, try again with an elevated Command Prompt:
- User-related:
	- ```git config --global user.name <username>``` (same username as your GitHub profile);
	- ```git config --global user.email <email>``` (same email as your GitHub verified email address);
	- ```git config --global user.signingkey <sec-key-ID>```.
- GPG-related:
	- If key management was done on Git Bash: ```git config --global gpg.program "<drive>:\<programs>\Git\usr\bin\gpg.exe"```;
	- On Command Prompt: ```git config --global gpg.program "<drive>:\<programs>\GnuPG\bin\gpg.exe"```.
- Version control-related:
	- ```git config --global commit.gpgsign true``` (automatically signs commits).
	
The Git configuration procedure is now complete. You can close the window.

#### Stage, commit, and push using Git

To change the repository with files that aren't compatible with your IDE (CAD files, for instance), simply follow this procedure in a Git Bash window opened in your repository clone directory:

```bash
# Stage changes
git add .

# Check new and modified files for approval
git status

# Commit with message
git commit -a -m <msg> # or simply 'git commit -a', to open a multiline commit message in your default text editor

# Push in the right branch
git push origin <branch>
```

For more option or a deeper understanding of Git and its commands, refer to the [Git documentation](https://git-scm.com/docs).

[//]: # (------------------------------------------------)

## IDE Configuration

#### Git on VSCode / VSCodium

To configure Git in VSCode / VSCodium, open one IDE and follow these steps:
- Extensions (<kbd>Ctrl</kbd>+<kbd>Shift</kbd>+<kbd>X</kbd>): Make sure that the "Git Extension Pack" extension is installed (and any other Git extension you find useful);
- File &#8594; Preferences &#8594; Settings (<kbd>Ctrl</kbd>+<kbd>,</kbd>) &#8594; Extensions &#8594; Git &#8594; Enable Commit Signing;
	- Alternatively, Show All Commands (<kbd>Ctrl</kbd>+<kbd>Shift</kbd>+<kbd>P</kbd>) &#8594; Preferences: Open settings (JSON) &#8594; Add: ```"git.enableCommitSigning": true```. You can also add the command to the workspace JSON settings, it will override the user defaults. If you set it in the workspace, make sure every collaborator has setup their KMS, else the command will prevent them from committing to the repository.

#### Arduino on VSCode / VSCodium	

To configure Arduino in VSCode / VSCodium, follow these steps:
- Make sure that you install the [Arduino IDE](#insIDE): the Arduino extension on VSCode / VSCodium will need its executables;
- Find your Arduino path file ("<drive:\<programs>\Arduino", for instance) and add the [Sunfounder PWM Servo Driver library](../README.md#PWM) to the Arduino libraries ("<drive>:\<programs>\Arduino\libraries" with folder name "Adafruit_PWMServoDriver", for instance). This step is specific to our project;
- On VSCode or VSCodium;
	- Extensions (<kbd>Ctrl</kbd>+<kbd>Shift</kbd>+<kbd>X</kbd>): Make sure that the "Arduino" extension is installed (and any other Arduino/C/C++ extension you find useful);
	- Show All Commands (<kbd>Ctrl</kbd>+<kbd>Shift</kbd>+<kbd>P</kbd>) &#8594; Preferences: Open settings (JSON) &#8594; Add the following parameters (according to the [VSCode Arduino extension's GitHub page](https://github.com/microsoft/vscode-arduino)): 
		```bash
		"arduino.path": "<drive>:\\<programs>\\Arduino",
		"arduino.commandPath": "arduino_debug.exe",
		"arduino.logLevel": "info", 
		"arduino.enableUSBDetection": true,
		"arduino.disableTestingOpen": false,
		"arduino.skipHeaderProvider": false,
		"arduino.additionalUrls": [
		"https://raw.githubusercontent.com/VSChina/azureiotdevkit_tools/master/package_azureboard_index.json",
		"http://arduino.esp8266.com/stable/package_esp8266com_index.json"
		],
		"arduino.defaultBaudRate": 115200
		```

	- Inside your workspace's ".vscode" folder, add the file "arduino.json" and write the following parameters:
		```bash
		{
		    "port": "<port_name>",
		    "board": "arduino:avr:<type>",
		    "configuration": "cpu=<cpu_type>",
		    "sketch": "<file_directory>\\<file_name>.ino"
		}
		```
	- Still in the same folder, add the file "c_cpp_properties.json" and write the following parameters:
		```bash
		{
		    "configurations": [
			{
			    "name": "Win32",
			    "includePath": [
				"${workspaceFolder}\\**",
				"<drive>:\\<programs>\\Arduino\\tools\\**",
				"<drive>:\\<programs>\\Arduino\\libraries\\**",
				"<drive>:\\<programs>\\Arduino\\hardware\\arduino\\avr\\**",
				"<drive>:\\<programs>\\Arduion\\hardware\\arduino\\avr\\cores\\arduino",
				"<drive>:\\<programs>\\Arduino\\hardware\\arduino\\avr\\libraries\\EEPROM\\src",
				"<drive>:\\<programs>\\Arduino\\hardware\\arduino\\avr\\libraries\\HID\\src",
				"<drive>:\\<programs>\\Arduino\\hardware\\arduino\\avr\\libraries\\SoftwareSerial\\src",
				"<drive>:\\<programs>\\Arduino\\hardware\\arduino\\avr\\libraries\\SPI\\src",
				"<drive>:\\<programs>\\Arduino\\hardware\\arduino\\avr\\libraries\\Wire\\src",
				"<drive>:\\<programs>\\Arduino\\hardware\\arduino\\avr\\libraries\\SPI\\src"
			    ],
			    "defines": [
				"_DEBUG",
				"UNICODE",
				"_UNICODE",
				"F_CPU=16000000L",
				"ARDUINO=10805",
				"ARDUINO_AVR_UNO",
				"ARDUINO_ARCH_AVR"
			    ],
			    "compilerPath": "<drive>:\\<programs>\\Arduino\\hardware\\tools\\avr\\bin\\avr-gcc.exe",
			    "cStandard": "c11",
			    "cppStandard": "c++17",
			    "intelliSenseMode": "msvc-x64",
			    "forcedInclude": [
				"<drive>:\\<programs>\\Arduino\\hardware\\arduino\\avr\\cores\\arduino\\Arduino.h"
			    ]
			}
		    ],
		    "version": 4
		}
		```
	
The IDE configuration procedure is now complete. You can close the window.

[//]: # (------------------------------------------------)

##
That's it! You should have integrated Git and Arduino into your favorite IDE now, and allowed a KMS to sign your commits. You have also upgraded the Python version on your Raspberry Pi. If any issue persists, you can find help online on Stack Overflow, the GitHub forums, and more.

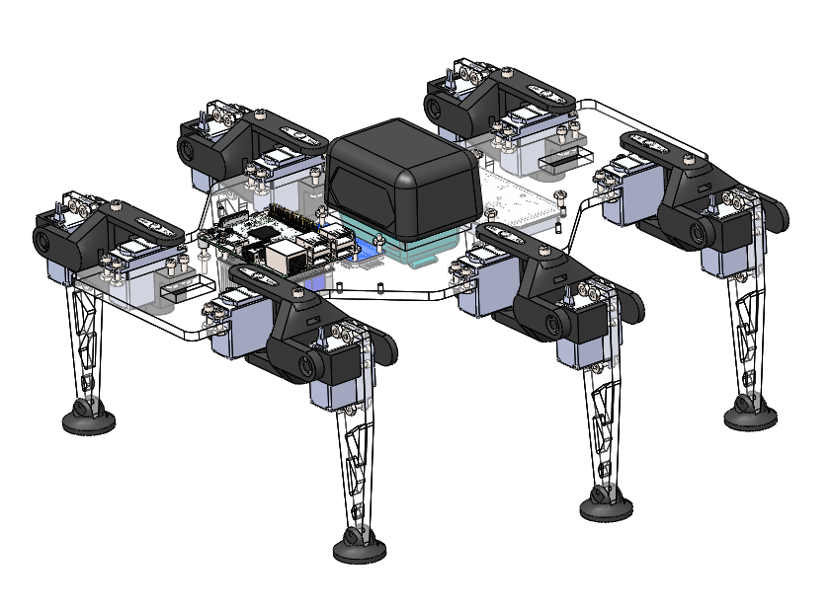
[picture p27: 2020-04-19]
img/robot_assembly.png

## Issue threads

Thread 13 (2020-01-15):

Interface de contrôle

Philbrad99, 2020-01-15:
Création d'un interface lié au programme de contrôle du robot

Philbrad99, 2020-01-29:
Vu l'ampleur du travail de l'interface, il fera partie du sprint 2 et 3 en plus du sprint 4.

Closed 2020-02-11.

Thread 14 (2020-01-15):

Simulation du mouvement

Philbrad99, 2020-01-15:
Simuler le déplacement du robot pour optimiser les mouvements

Philbrad99, 2020-02-05:
Il ne sera pas nécessaire de faire une simulation du mouvement pour les fonctionnalités désirées.

Closed 2020-02-05.

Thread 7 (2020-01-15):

Assemblage

Philbrad99, 2020-01-15:
Ajout des pattes au corps et fixations des pièces électroniques

Closed 2020-02-24.

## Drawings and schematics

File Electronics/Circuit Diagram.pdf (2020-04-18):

8A/100W

## MAX 12A

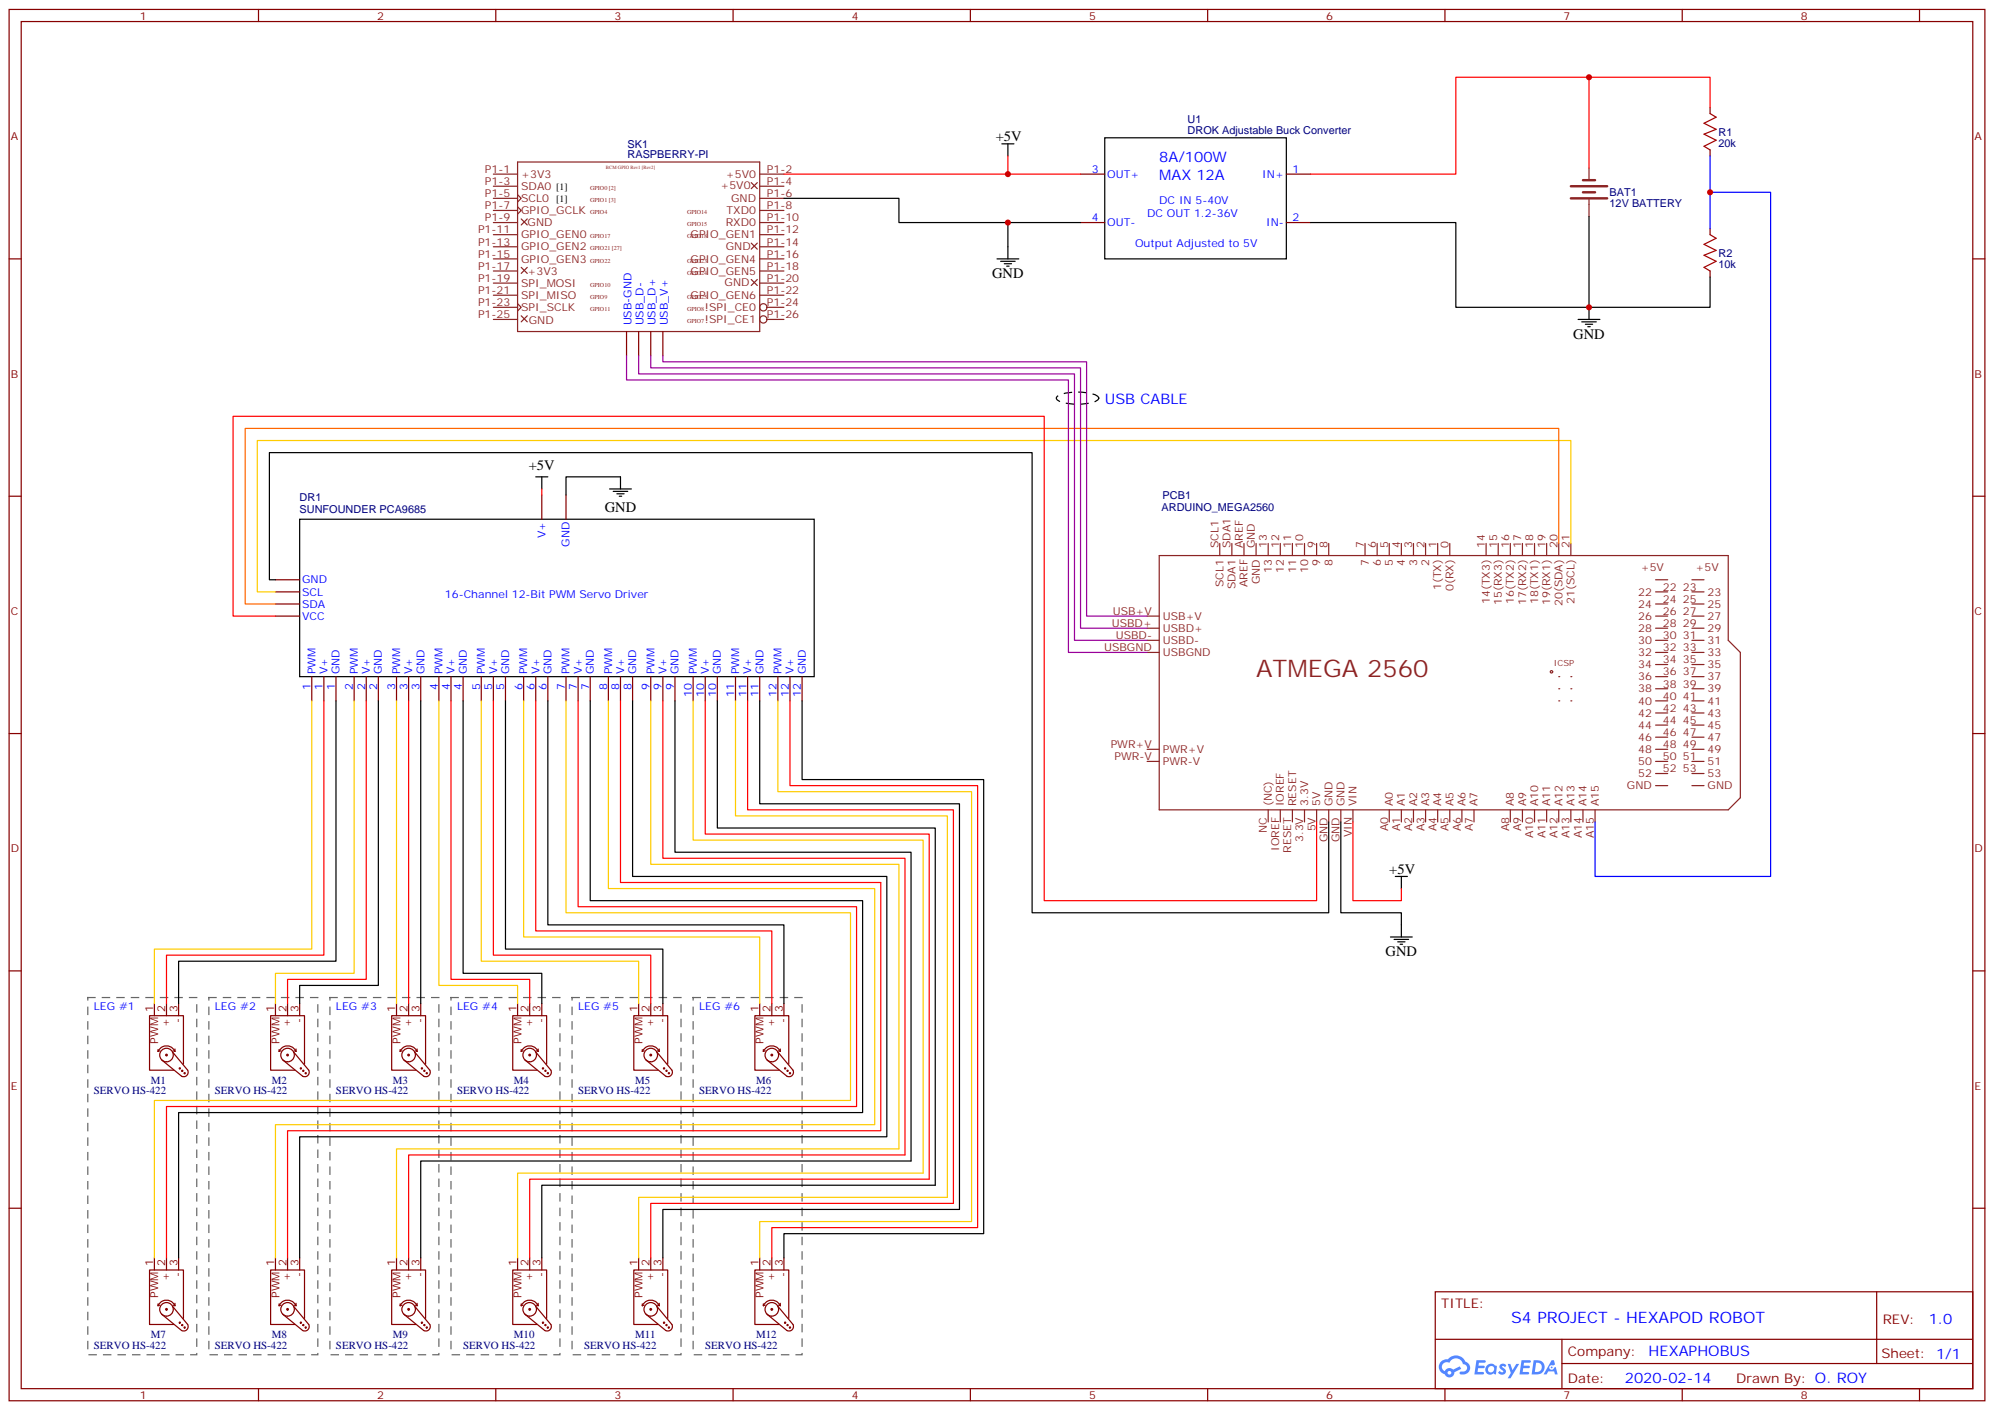
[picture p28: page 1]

DROK Adjustable Buck Converter

16-Channel 12-Bit PWM Servo Driver

VIN VIN GND GND GND GND 5V 5V 3.3V 3.3V RESET RESET IOREF IOREF (NC) NC

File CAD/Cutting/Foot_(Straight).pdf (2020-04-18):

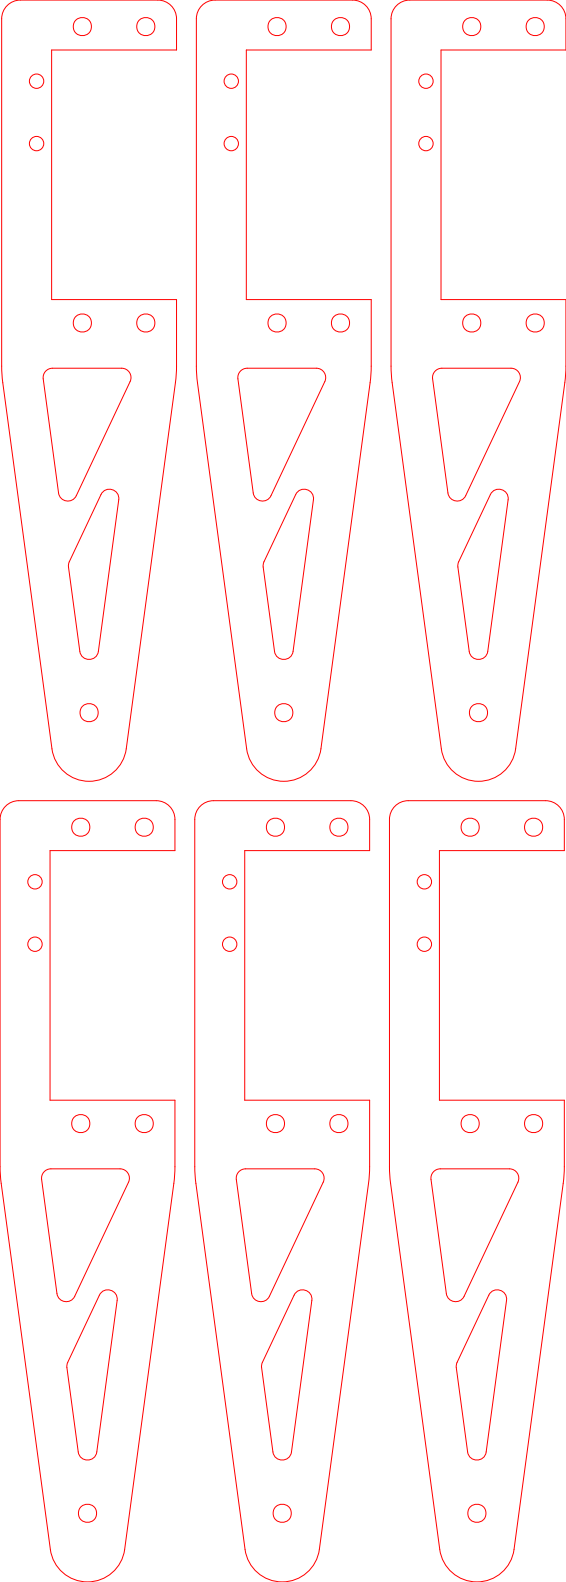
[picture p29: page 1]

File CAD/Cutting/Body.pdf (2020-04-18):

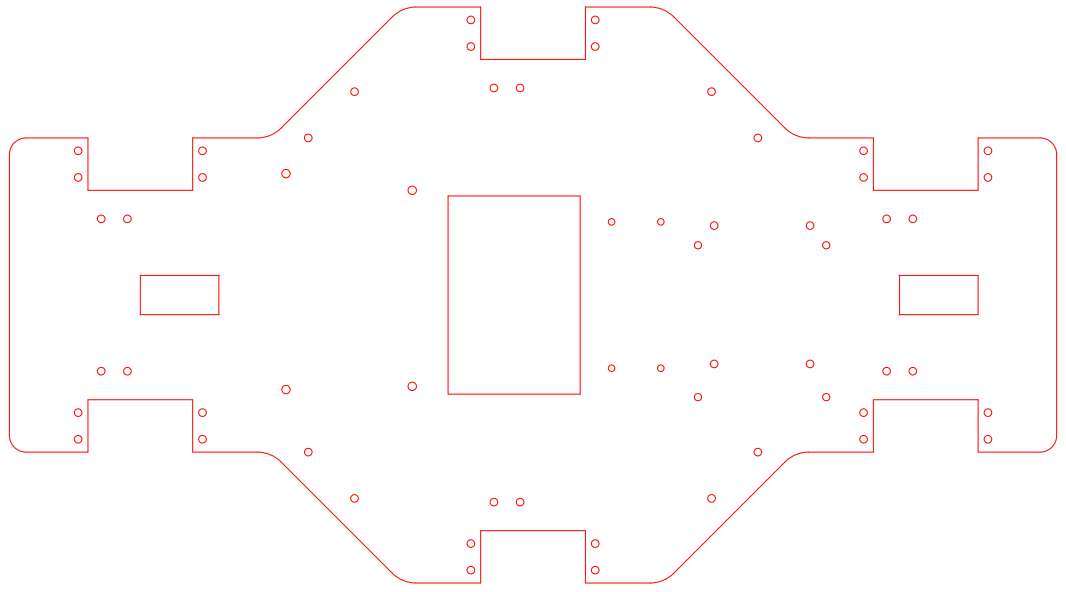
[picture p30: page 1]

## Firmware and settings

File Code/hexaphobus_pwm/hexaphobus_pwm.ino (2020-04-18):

/*!
 * @file hexaphobus_pwm.ino
 * 
 * @authors
 *          - Cabana,       Gabriel  | cabg2101
 *          - Guay-Tanguay, Carolane | guac3201
 *          - Lalonde,      Philippe | lalp2803
 *          - Roy,          Olivier  | royo2206
 * 
 * @date
 *       - 2020-01-29 (Creation)
 *       - 2020-04-18 (Last modification)
 * 
 * Motion control, communication, and sequencing (main).
 * 
 * <b>S4-H20 | GRO400</b>
 */

/*!
 * @page page_ino PWM on Arduino
 *
 * @section intro_sec Introduction
 *          Arduino code designed for intuitive control and monitoring of the
 *          HexaphobUS robot. 
 * 
 *          The servomotors use an I2C-bus controller
 *          (<a href="http://wiki.sunfounder.cc/index.php?title=PCA9685_16_Channel_12_Bit_PWM_Servo_Driver">
 *          Sunfounder PCA9685</a>) to communicate, with a 12-bit resolution
 *          (4096 steps).
 *
 * @section dependencies Dependencies
 *          This library depends on
 *          <a href="https://github.com/adafruit/Adafruit-PWM-Servo-Driver-Library">
 *          Adafruit PWM Servo Driver Library</a> being present on your system.
 *          Please make sure you have installed the latest version before using
 *          this library.
 *
 * @section license License
 *          This falls under the GitHub repository license (GPLv3). See more
 *          <a href="https://github.com/gabrielcabana21/HexaphobUS/blob/master/LICENSE">
 *          here</a>. 
 */

/********************************************/

#  include <Wire.h>
#  include <Adafruit_PWMServoDriver.h>
#  include <Arduino.h>
///< Header of custom functions.
#  include "hexaphobus_pwm.h" 

/********************************************/

/// Servomotor counter.
uint8_t servonum = 0;
/// State of the robot. 
int State = 0;

/********************************************/

/*!
 * @brief Sets up the Arduino Mega 2560 R3.
 * 
 *        This function sets the serial data transmission, the I2C
 *        communication with the PWM servo driver, and the update
 *        frequency.
 */
void setup() {

  Serial.begin(9600);
  pwm.begin();
  pwm.setPWMFreq(FREQUENCY);
  delay(1000);
  init_move();
}

/*!
 * @brief Runs the Arduino Mega 2560 R3.
 * 
 *        This function calibrates the servomotors and allows the robot
 *        to move according to user input.
 */
void loop() { 
  
  State = UpdateCommand();

  if (State != 0 && State != -1) {
    if (State == 1) {
      Moving(POS_FRONT);
    }
    else if (State == 2) {
      Moving(POS_BACK);
    }
    else if (State == 3) {
      MovingLeft();
    }
    else if (State == 4) {
      MovingRight();
    }
    AngleToHMI();
    State = 0;
  }
}

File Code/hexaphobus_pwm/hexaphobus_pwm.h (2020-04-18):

/*!
 * @file hexaphobus_pwm.h
 * 
 * @authors
 *          - Boulet,       Philippe | boup2341
 *          - Cabana,       Gabriel  | cabg2101
 *          - Guay-Tanguay, Carolane | guac3201
 *          - Lalonde,      Philippe | lalp2803
 *          - Roy,          Olivier  | royo2206
 * 
 * @date
 *       - 2020-02-25 (Creation)
 *       - 2020-04-18 (Last modification)
 * 
 * Motion control, communication, and sequencing (header).
 * 
 * <b>S4-H20 | GRO400</b>
 */

/********************************************/

#  include <Adafruit_PWMServoDriver.h>

/// Encoder value (min).
#  define MIN_PULSE_WIDTH     650
/// Encoder value (max).
#  define MAX_PULSE_WIDTH     2650
/// Encoder value (calibrated zero).
#  define DEFAULT_PULSE_WIDTH 1500
/// Communication frequency.
#  define FREQUENCY           50

/// Position value (down).
#  define POS_DOWN   0
/// Position value (up).
#  define POS_UP     1
/// Position value (back).
#  define POS_BACK   0
/// Position value (front).
#  define POS_FRONT  1
/// Position value (center).
#  define POS_CENTER 2

/// Angle value in degrees (down).
#  define DOWN   65-15
/// Angle value in degrees (up).
#  define UP     25-15
/// Angle value in degrees (back).
#  define BACK   10
/// Angle value in degrees (front).
#  define FRONT  75
/// Angle value in degrees (center).
#  define CENTER 43

/// Flag for reading new data.
boolean newData = false;
/// Bytes transferred via serial communication.
String input_string;
/// State to be executed according to movement command.
int return_state = 0;

/// Adjustments for each servomotor angle.
int SHIFT[13] = {-1, -10, -5, 0, 0, -5, 5, 56, 68, 58, 56, 56, 68};
/// Servomotor angles.
int ANGLE[13] = {-1, 0, 0, 0, 0, 0, 0, 0, 0, 0, 0, 0, 0};

/// Communication port with the PWM servo driver.
Adafruit_PWMServoDriver pwm = Adafruit_PWMServoDriver();

/********************************************/

/*!
 * @brief Writes command to the communication port.
 * 
 *        The command written to the port should be 1 for a forward
 *        movement, 2 for a backward movement, 3 for a left turn, and 4
 *        for a right turn.
 * 
 * @param string_to_write
 * 
 *        Movement state of the robot.
 */
void writeCommand(String string_to_write) {  
  Serial.println(string_to_write);
}

/*!
 * @brief Updates command to be written to the communication port.
 *        
 *        The updated command should be 1 for a forward movement, 2 for
 *        a backward movement, 3 for a left turn, and 4 for a right turn.
 * 
 * @return The command state for the next movement (integer).
 */
int UpdateCommand()
{
  while (newData == false) {
    input_string = "";
    input_string = Serial.readStringUntil('|');
    input_string = String(input_string);
    
    if (sizeof(input_string) > 0) {
      newData = true;
    } 
  }

  if (newData) {
    if (input_string == "FORWARD") {
      return_state = 1;
    }
    else if (input_string == "BACKWARD") {
      return_state = 2;
    }
    else if (input_string == "LEFT") {
      return_state = 3;
    }
    else if (input_string == "RIGHT") {
      return_state = 4;
    }
    else {
      newData = false;
      return -1;
    }

    newData = false;
    return return_state;
  }
  
  else {
    return_state = 0;
  }
  
  return 0;
}

/*!
 * @brief Sends servomotor angles to the HMI.
 *
 *       Prints the angle values in the terminal for each servomotor
 *       and sends the information to the HMI via serial communication.
 * 
 * @return 0 after communication with the HMI.
 */
int AngleToHMI() {
  
  String string_to_send = String(ANGLE[1]);

  for (int i = 2; i < 13; i++) {
    string_to_send += ";" + String(ANGLE[i]);
  }
  
  if (sizeof(string_to_send) < 6) {
    return -1;
  }
  writeCommand(string_to_send);
  return 0;
}

/********************************************/

/*!
 * @brief Converts an angle to a servomotor encoder value. 
 *
 *        Converts a desired angular position for a certain leg part
 *        to an encoder value for compatibility with the servomotors.
 * 
 * @param angle
 * 
 *        Desired angle for a specific servomotor.
 * 
 * @return analog_value, which is the servomotor encoder value.
 */
int pulseWidth(int angle) {
  if(angle > 180) {
    return -1;
  }
  
  int pulse_wide, analog_value;
  pulse_wide   = map(angle, 0, 180, MIN_PULSE_WIDTH, MAX_PULSE_WIDTH);
  analog_value = int(float(pulse_wide) / 1000000 * FREQUENCY * 4096);
  
  return analog_value;
}

/********************************************/

/*!
 * @brief Up and down movement sequence for the servomotors.
 *
 *        Moves up to three tibia servomotors (any motor from #1 to #6)
 *        up or down with the corresponding leg part.
 * 
 * @param Leg1
 * 
 *        First leg to move (any from #1 to #6). If leg parameter is
 *        equal to 0, the corresponding leg will not move.
 * 
 * @param Leg2
 * 
 *        Second leg to move (any from #1 to #6). If leg parameter is
 *        equal to 0, the corresponding leg will not move.
 * 
 * @param Leg3
 * 
 *        Third leg to move (any from #1 to #6). If leg parameter is
 *        equal to 0, the corresponding leg will not move.
 * 
 * @param pos1
 * 
 *        Direction of movement for the first leg.
 *        - POS_DOWN (0): move down;
 *        - POS_UP (1): move up.
 * 
 * @param pos2
 * 
 *        Direction of movement for the second leg.
 *        - POS_DOWN (0): move down;
 *        - POS_UP (1): move up.
 * 
 * @param pos3
 * 
 *        Direction of movement for the third leg.
 *        - POS_DOWN (0): move down;
 *        - POS_UP (1): move up.
 * 
 * @param Time
 * 
 *        Delay after sending the information to the servomotors.
 *        Crucial for optimized sequencing. 
 * 
 * @return -1 for handling errors, 0 if execution was correct.
 */
int UpAndDown(int Leg1,
              int Leg2,
              int Leg3,
              int pos1,
              int pos2,
              int pos3,
              int Time) {
  
  int Legs[3]  = {Leg1, Leg2, Leg3};
  int pos[3]   = {pos1, pos2, pos3};
  int angle[3] = {0, 0, 0};

  for (int i = 0; i < 3; i++) {
    if(Legs[i] > 0 && Legs[i] <= 6) {
      if (pos[i] == 1) {
        angle[i] = UP + SHIFT[Legs[i] + 6];
      }
      else {
        angle[i] = DOWN + SHIFT[Legs[i] + 6];
      }

      if (Legs[i] % 2 == 0) {
        pwm.setPWM(Legs[i] + 6, 0, pulseWidth(180 - angle[i]));
        ANGLE[Legs[i] + 6] = 180 - angle[i];
      }
      else if (Legs[i] == 0)
      {}
      else
      {
        pwm.setPWM(Legs[i] + 6, 0, pulseWidth(angle[i]));
        ANGLE[Legs[i] + 6] = angle[i];
      }
    }
    else if (Legs[i] == 0) {
    }
    else {
      return -1;
    }
  }

  delay(Time);
  return 0;
}
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

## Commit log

2020-01-22 First Version of LEG
    [Assembly.SLDASM, Attachement_Body.SLDPRT, Attachement_Patte.SLDPRT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]
2020-01-29 Servo motor PWM test on Arduino
2020-02-01 Graph now working with buttons
2020-02-05 Rename Code/license.txt to Code/Adafruit PWM Servo Driver Library/license.txt
2020-02-05 Rename Code/Adafruit PWM Servo Driver Library/pwmtest.pde to Code/Adafruit PWM Servo Driver Library/examples/pwmtest.pde
2020-02-05 Trying to frame tracking
2020-02-05 Added frame around graph and modify graph size when expanding
2020-02-05 Added the VSCode-Arduino setup method.
2020-02-05 Integration of Arduino build/verify in VSCode.
2020-02-05 Arduino update
2020-02-05 Arduino folder created.
2020-02-06 Added Arduino build to YAML (untested).
2020-02-06 Added voltage regulator information.
2020-02-06 Added battery information.
2020-02-07 Added all external CAD files.
    [12Channel PWM.SLDPRT, Batterie.SLDASM, DROK_090483.stp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]
2020-02-13 Modified tree structure of CAD files. Added body and mirrored leg.
    [12Channel PWM.SLDPRT, 1_2x2_56_Screws.SLDPRT, 1_2x4_40_Cap_Screws.SLDPRT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]
2020-02-13 Added external resources to main assembly. Modified the body.
    [Assembly_Leg_V3.SLDASM, Body.SLDPRT]
2020-02-13 Began fourth robot leg version.
    [Assembly_Leg_V2.SLDASM, Assembly_Leg_V3_Mirror.SLDASM, Assembly_Leg_V4.SLDASM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]
2020-02-14 New robot version, with new legs and new component layout.
    [Assembly_Leg_V3.SLDASM, Assembly_Leg_V4.SLDASM, Assembly_Leg_V4_Mirror.SLDASM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]
2020-02-14 Added procedure for direct stage, commit and push.
2020-02-14 Minor modification.
    [Assembly_Leg_V4.SLDASM]
2020-02-15 Added circuit diagram.
2020-02-19 Renamed files and modified body.
    [Assembly_Leg_V2.SLDASM, Assembly_Leg_V3.SLDASM, Assembly_Leg_V3_Mirror.SLDASM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]
2020-02-19 Moved parts to external folder.
    [Leg.SLDASM, Leg_(Mirror).SLDASM]
2020-02-19 Update Foot and Body Cut files
    [Body.DXF, Foot.DXF]
2020-02-19 Calibration function added
2020-02-20 Update calibration function
2020-02-20 Added fasteners.
    [Body.SLDPRT, Leg.SLDASM, Leg_(Mirror).SLDASM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]
2020-02-20 Added motor position shifts after testing.
2020-02-25 Added next-gen leg design for more powerful motors.
    [Bearing_mount_(Femur).SLDPRT, Bearing_mount_(Foot).SLDPRT, Body.SLDPRT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]
2020-02-25 test for arduino
2020-02-25 New foot version (Foot_V2_Straight)
    [Foot_V2_Straight.SLDPRT]
2020-02-25 Added a header for Arduino code
2020-02-25 Renamed files for clarity.
    [Femur.SLDASM, Femur_(Mirror).SLDASM, Foot+Femur.SLDASM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]
2020-02-25 calibration of coxa motors.
2020-02-26 Updated next-gen CAD files.
    [Femur.SLDASM, Femur_(Mirror).SLDASM, Foot+Femur.SLDASM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]
2020-02-26 Added print-oriented femur-to-tibia joint CAD file.
    [Joint_(Femur_to_tibia)_(Print).SLDPRT]
2020-03-09 Function to move legs one at time added
2020-03-09 Arduino code update
2020-03-11 Minor CAD update.
    [Foot+Tibia+Femur.SLDASM, Joint_(Femur_to_tibia)_(Print)_(Mirror).SLDPRT]
2020-03-11 Reduce length of straight feet
    [Foot_V2_Straight.SLDPRT]
2020-03-11 Cut file for straight foot
    [Foot_V2_Straight.DXF]
2020-03-18 added moving legs to graph
2020-03-19 Added Python configuration.
    Added a method to install the Python source code on Debian 9 (Raspberry Pi 3+) to run the latest version and avoid issues with the user interface and serial communication.
2020-03-19 Modified YAML config for Arduino.
2020-03-19 Modified serial communication in thread
2020-03-24 Modified Arduino documentation according to Doxygen guidelines.
2020-03-25 timer call for function for serial comm
2020-04-08 Building of V2 with new splippers and a shell
    [Batterie_holder.SLDPRT, Bearing_mount_leg.SLDPRT, Body.SLDPRT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]
2020-04-08 Minor edits to file names and binaries.
    [Body.SLDPRT, Foot.SLDPRT, Foot_(Curved).SLDPRT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]
2020-04-08 Minor edits.
    [Foot_(Straight).SLDPRT, Leg_(Straight_Foot).SLDASM, Slippers.SLDPRT]
2020-04-18 Construction of the shell of the robot and adjusting the slippers.
    [Leg_(Straight_Foot).SLDASM, Leg_(Straight_Foot)_(Mirror).SLDASM, Shell_back.SLDPRT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]
2020-04-18 clean function arduino
2020-04-18 Updated CAD file names and links.
    [Foot.DXF, Foot_(Curved).DXF, Foot_(Straight).DXF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]
2020-04-19 Photo of CAD added
2020-04-19 Picture of the final robot assembly
2020-04-22 Added SVGs and a V3 CAD assembly.
    [Batterie_holder.SLDPRT, Battery_holder.SLDPRT, Bearing_mount_(Femur).SLDPRT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]
2020-04-22 Trimmed CAD folder contents and added BOM.
    [BOM.xlsx, Leg_(Curved_Foot).SLDASM, Leg_(Curved_Foot)_(Mirror).SLDASM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]
2020-04-22 Updated BOM.
    [BOM.xlsx, Leg_(Curved_Foot).SLDASM, Leg_(Curved_Foot)_(Mirror).SLDASM]
2020-04-23 BOM completed, fasteners added to CAD files.
    [BOM.xlsx, Body_(Small).SLDPRT, Femur.SLDASM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]
2020-10-05 Added images of V3 CAD.
2020-10-09 Added images of V1/V2 CAD.
